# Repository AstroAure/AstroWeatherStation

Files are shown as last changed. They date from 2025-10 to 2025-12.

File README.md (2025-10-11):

# AstroWeatherStation

**AstroWeatherStation** is an open-source weather station that aims at providing a low-cost (~100€) alternative to commercial ones. It also offers full flexibility to how your data are stored and accessed, as well as the possibility to add whatever sensor you want.

To leave a telescope outside permanently (under a dome, or with a waterproof telescope), one needs a weather station to observe the environmental conditions. This allows the telescope to be put in a safe mode if they are dangerous (e.g. rain or dew), or simply to know if observation is possible (absence of clouds).

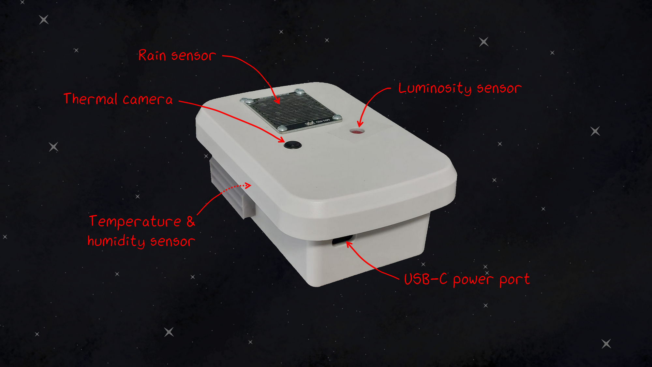
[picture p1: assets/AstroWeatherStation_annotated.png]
Annotated picture of AstroWeatherStation. It is a white box with multiple sensors (rain, luminosity, temperature&humidity and thermal camera) and a USB-C power port.


## Features

AstroWeatherStation hosts multiple different sensors:
* DHT22: Temperature and humidity sensor
* MH-RD: Rain sensor
* MLX90640 110deg: IR Thermal camera (for cloud detection)
* TSL2591: Luminosity sensor (for start/end of observation at dawn/dusk and darkness of night measurement)

It uses the [Grove ecosystem](https://wiki.seeedstudio.com/Grove_System/) to easily connect sensors without any soldering. Sensors that don't use this ecosystem (like the TSL2591 and the MH-RD sensors) can still be connected by using the appropriate adapter cables. AstroWeatherStation uses an ESP32 controller with the Grove Shield and the Grove I2C hub which provides plenty of ports to connect sensors (digital, analog, I2C, UART).

## Hardware

| Component | Quantity | Price | Description |
| :-: | :-: | :-: | :-: |
| [XIAO ESP32-C6 board](https://www.seeedstudio.com/Seeed-Studio-XIAO-ESP32C6-Pre-Soldered-p-6328.html) | 1 | 5.30€ | Controller |
| [Grove Shield](https://www.seeedstudio.com/Grove-Shield-for-Seeeduino-XIAO-p-4621.html) | 1 | 3.90€ | Shield for the ESP32 board |
| [Grove I2C Hub](https://www.seeedstudio.com/Grove-I2C-Hub-6-Port-p-4349.html) | 1 | 1.50€ | Additional I2C ports |
| [DHT22 sensor](https://www.seeedstudio.com/Grove-Temperature-Humidity-Sensor-Pro-AM2302-DHT22.html) | 1 | 7.00€ | Temperature & humidity sensor |
| [MLX90640 110deg](https://www.seeedstudio.com/Grove-Thermal-Imaging-Camera-IR-Array-MLX90640-110-degree-p-4334.html) | 1 | 43.00€ | IR Thermal camera |
| [MH-RD sensor](https://www.berrybase.ch/fr/detail/019234a3bb007361a022dfc33cb3b6cc) | 1 | 1.90€ | Rain sensor |
| [TSL2591 sensor](https://www.berrybase.ch/adafruit-tsl2591-high-dynamic-range-digitaler-licht-sensor) | 1 | 7.50€ | Luminosity sensor |
| [CHD7310WH enclosure](https://www.camdenboss.com/camden-boss/chd7310wh-73-series-ip68-waterproof-enclosure%2C-white%2C-asa-ul94hb%2C-150x100x55mm/c-23/p-24506) | 1 | 25.40€ | Waterproof enclosure |
| [Grove cable](https://www.seeedstudio.com/Grove-Universal-4-Pin-Buckled-20cm-Cable-5-PCs-pack.html) | 3 | 1.70€ | Sensor connection |
| [Grove-Jumper cable](https://www.seeedstudio.com/Grove-4-pin-Female-Jumper-to-Grove-4-pin-Conversion-Cable-5-PCs-per-PAck.html) | 1 | 3.00€ | MH-RD sensor connection |
| [Grove-Qwiic cable](https://www.berrybase.ch/sparkfun-qwiic-grove-adapterkabel-100mm) | 1 | 2.00€ | TSL2591 sensor connection
| [USB-C cable](https://www.berrybase.ch/en/detail/019234a6a33a7045b0129025e8e15021) | 1 | 2.80€ | Power cable
| [Stevenson screen](/hardware/3d-printing/) | 4 | 3D printed | Rain-proof ventilation for inside sensors |
| [MLX90640 support](/hardware/3d-printing/MLX90640%20Support.3mf) | 1 | 3D printed | Support for the MLX90640 thermal camera |
| [TSL2591 support](/hardware/3d-printing/TSL2591%20Support.3mf) | 1 | 3D printed | Support for the TSL2591 sensor |
| [Base plate](/hardware/laser-cutting/Base%20plate.dxf) | 1 | Laser cut | Base plate to hold the electronics

## Code

### ESP32

The weather station is controlled by an ESP32 board ([XIAO ESP32-C6 model](https://www.seeedstudio.com/Seeed-Studio-XIAO-ESP32C6-p-5884.html)). The code, written in MicroPython, for it can be found in [this folder](code/esp32/). It hosts:
* [`boot.py`](code/esp32/boot.py): The booting code which connects the weather station to a WiFi network. If no known network is found, it will host its own WiFi network where you will be able to setup the connection.
* [`main.py`](code/esp32/main.py): The main code that reads the sensor values and upload their values to the `index.html` page.
* [`index.html`](code/esp32/index.html): The raw HTML page that shows the sensor values of the weather station. It is formatted to be used by the [WeatherWatcher INDI library](https://indilib.org/weather/weather-watcher.html), but it can be easily used with an other standard.
* Libraries: [`mlx90640.py`](code/esp32/mlx90640.py), [`tsl2591.py`](code/esp32/tsl2591.py), [`wifimgr.py`](code/esp32/wifimgr.py)
* Test code for individual sensors: [`test_dht22.py`](code/esp32/test/test_dht22.py), [`test_mhrd.py`](code/esp32/test/test_mhrd.py), [`test_mlx90640.py`](code/esp32/test/test_mlx90640.py), [`test_tsl2591.py`](code/esp32/test/test_tsl2591.py)

### RaspberryPi

The weather station publishes its sensor values to an HTML page on the WiFi network to which it is connected. The [`log_astroweatherstation.py`](code/raspberrypi/log_astroweatherstation.py) program recovers the sensor values from this page and sends them to an InfluxDB database to store them. From there, they can be plotted in Grafana for example. This code also saves the IR thermal camera data as an image and in a log file for post-processing.

* To install InfluxDB and Grafana on a RaspberryPi, follow [this tutorial](https://sandyjmacdonald.github.io/2021/12/29/setting-up-influxdb-and-grafana-on-the-raspberry-pi-4/).

* To run the logging code on your RaspberryPi every minute to log the weather station data, you can use the `crontab -e` command and add the following line, where `<PATH-TO-FILE>` should be changed with the absolute path to the Python file:

    ```
    */1 * * * * /usr/bin/python3 <PATH-TO-FILE>/log_astroweatherstation.py &
    ```

## References

* [`wifimgr.py`](https://github.com/tayfunulu/WiFiManager) by [Tayfun ULU](https://github.com/tayfunulu): WiFi manager library *(MIT License)*
* [`tsl2591.py`](https://github.com/mchobby/esp8266-upy/tree/master/tsl2591) by [MCHobby](https://github.com/mchobby): MicroPython library for TSL2591 luminosity sensor *(MIT License)*
* Auto-gain for `tsl2591.py` by [Aurélien Genin](https://github.com/AstroAure) *(MIT License)*
* [`mlx90640.py`](https://github.com/michael-sulyak/micropython-mlx90640) by [Michael Sulyak](https://github.com/michael-sulyak): MicroPython library for MLX90640 IR thermal camera *(MIT License)*

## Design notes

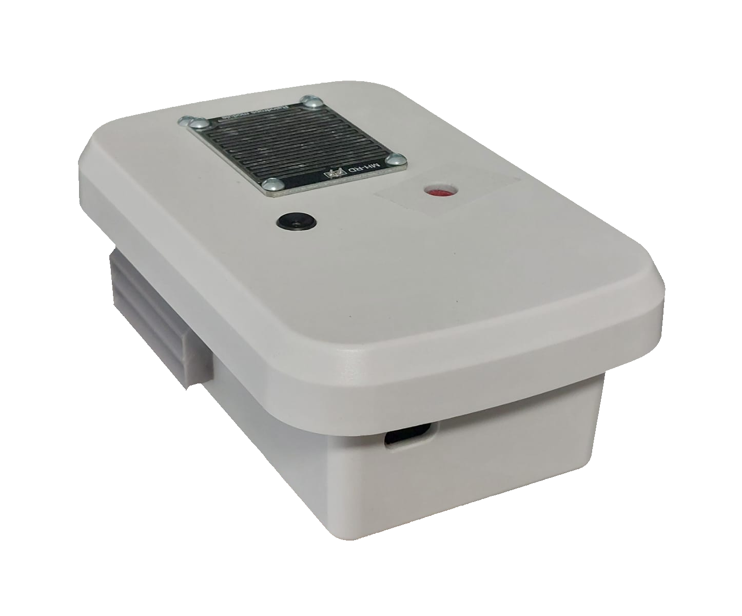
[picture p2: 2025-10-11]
assets/AstroWeatherStation_transparent.png

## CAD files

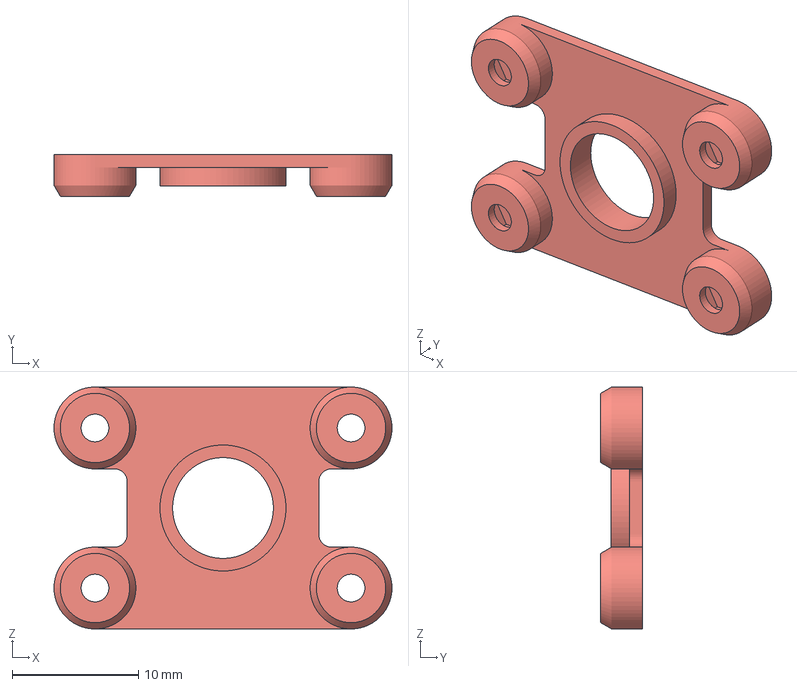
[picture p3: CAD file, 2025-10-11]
hardware/3d-printing/TSL2591 Support.3mf
26.8 x 3.30 x 19.2 mm

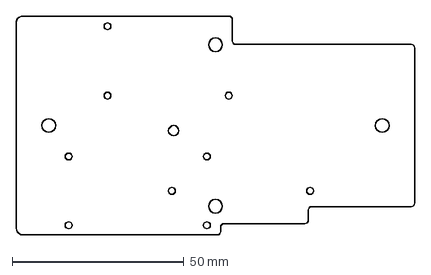
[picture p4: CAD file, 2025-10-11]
hardware/laser-cutting/Base plate.dxf
115.9 x 63.7 mm

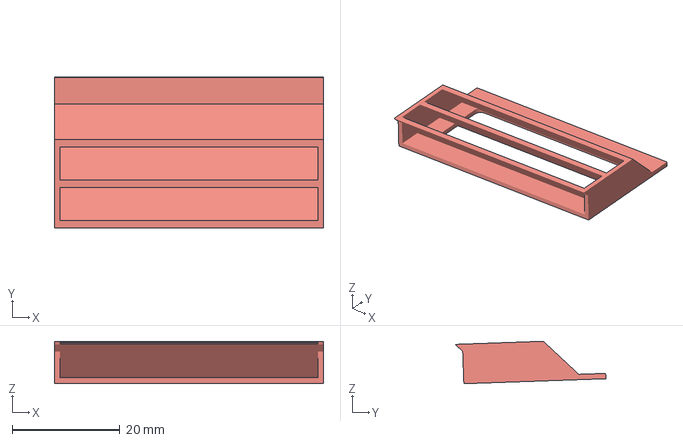
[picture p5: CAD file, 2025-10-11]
hardware/3d-printing/Stevenson Screen 1.3mf
50.0 x 28.0 x 7.89 mm

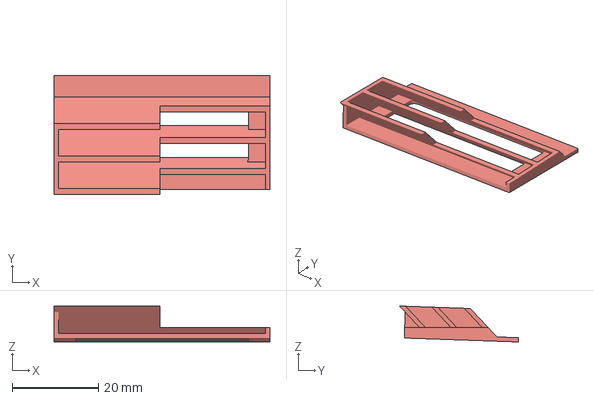
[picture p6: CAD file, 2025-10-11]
hardware/3d-printing/Stevenson Screen 4.3mf
50.0 x 27.5 x 8.33 mm

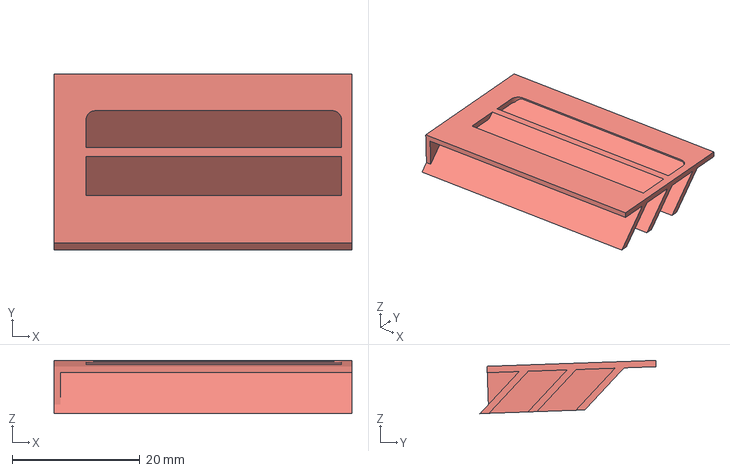
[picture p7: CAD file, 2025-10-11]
hardware/3d-printing/Stevenson Screen 3.3mf
46.6 x 27.5 x 8.33 mm

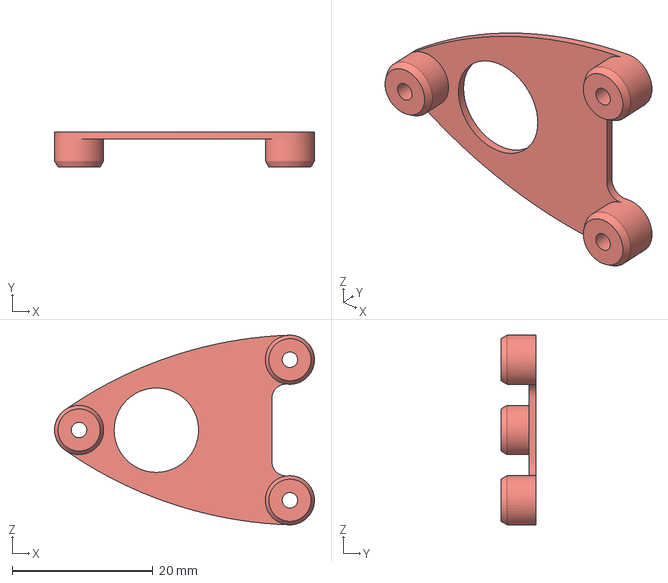
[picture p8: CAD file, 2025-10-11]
hardware/3d-printing/MLX90640 Support.3mf
37.0 x 5.00 x 27.0 mm

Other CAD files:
hardware/3d-printing/Stevenson Screen 2.3mf

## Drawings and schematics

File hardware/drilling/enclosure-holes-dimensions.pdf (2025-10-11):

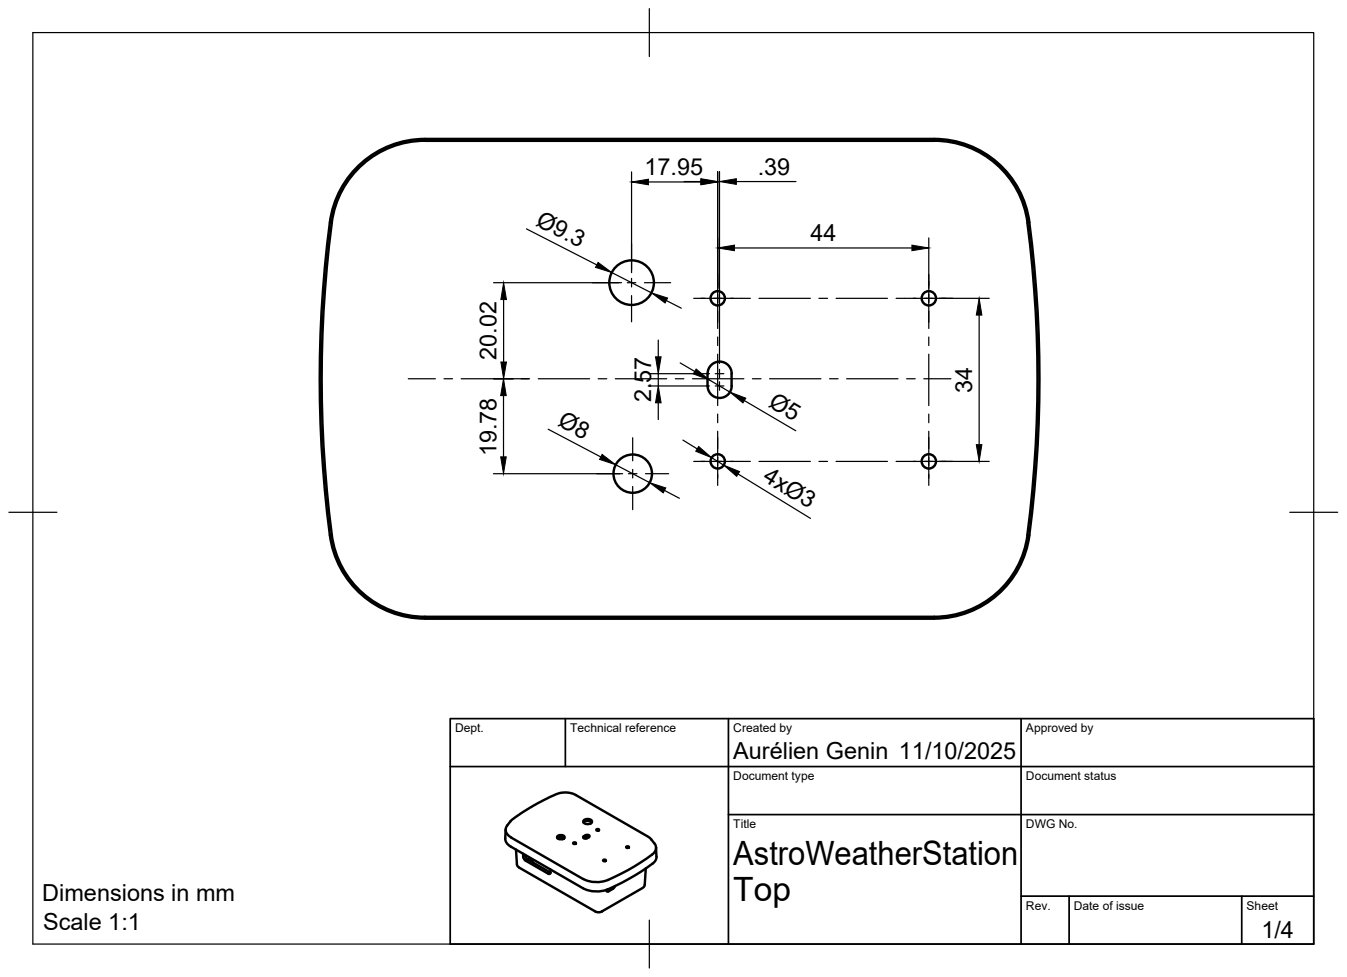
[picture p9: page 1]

Dept. | Technical reference | Created by Aurélien Genin 11/10/2025 | Approved by

Document type | Document status

Title AstroWeatherStation Top | DWG No.

Dimensions in mm
Scale 1:1

Rev. | Date of issue | Sheet

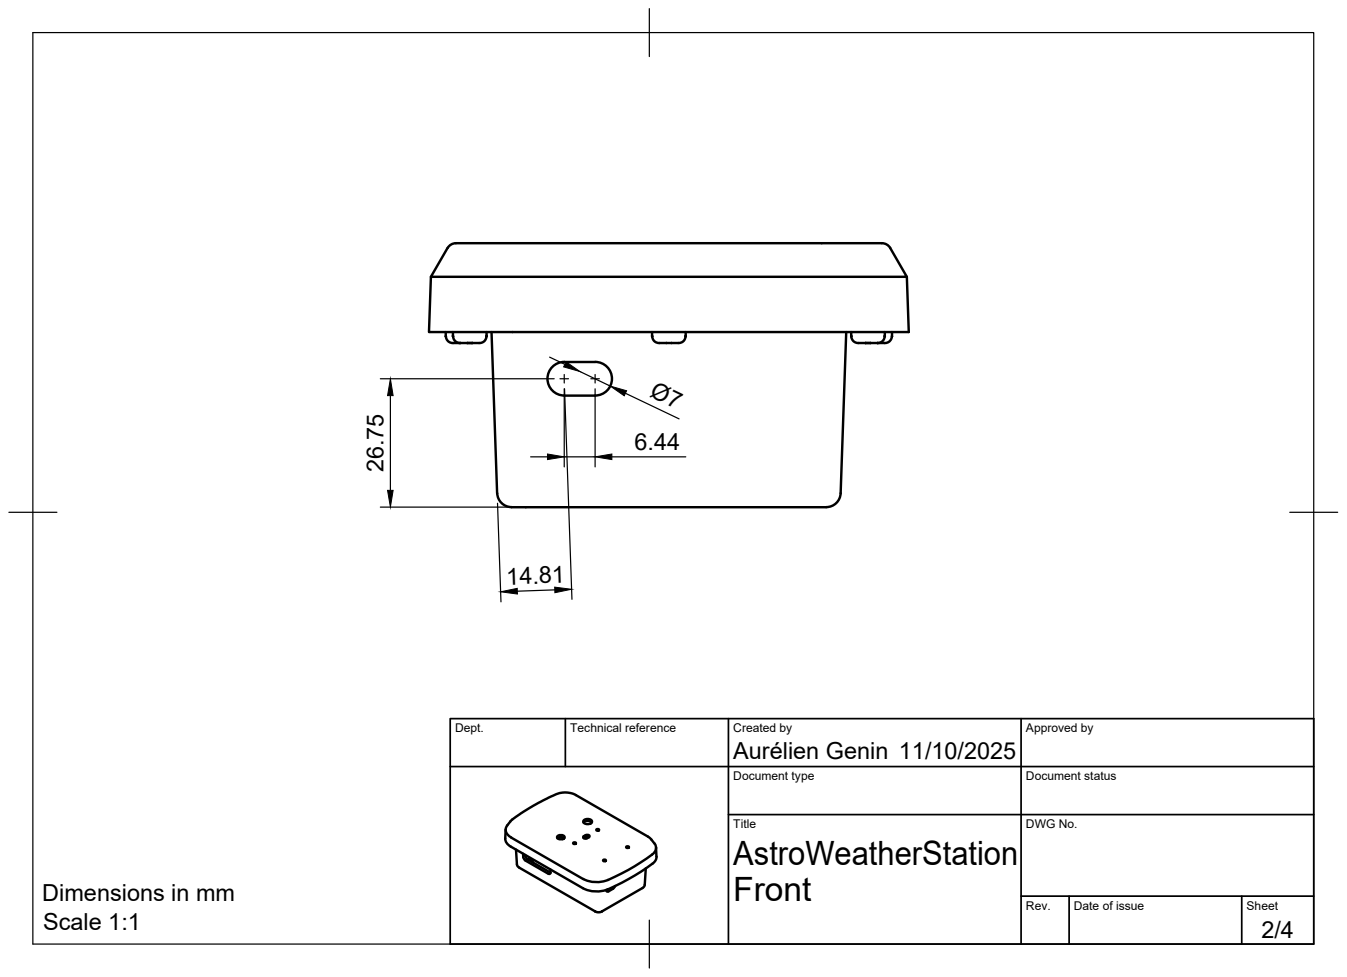
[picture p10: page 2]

Dept. | Technical reference | Created by Aurélien Genin 11/10/2025 | Approved by

Document type | Document status

Title AstroWeatherStation Front | DWG No.

Dimensions in mm

Rev. | Date of issue | Sheet

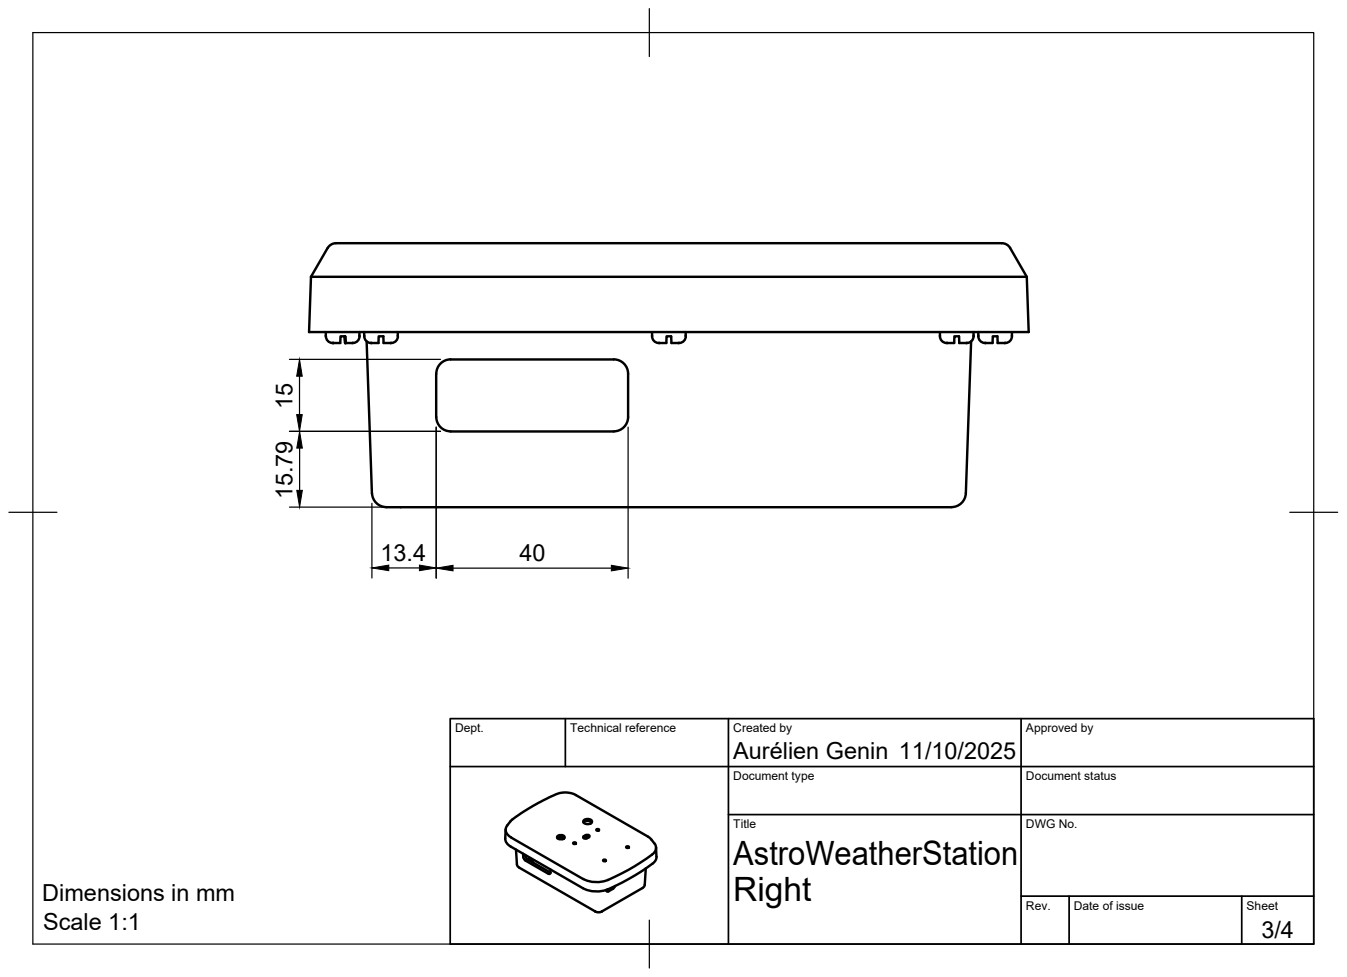
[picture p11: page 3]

Dept. | Technical reference | Created by Aurélien Genin 11/10/2025 | Approved by

Document type | Document status

Title AstroWeatherStation Right | DWG No.

Dimensions in mm

Rev. | Date of issue | Sheet

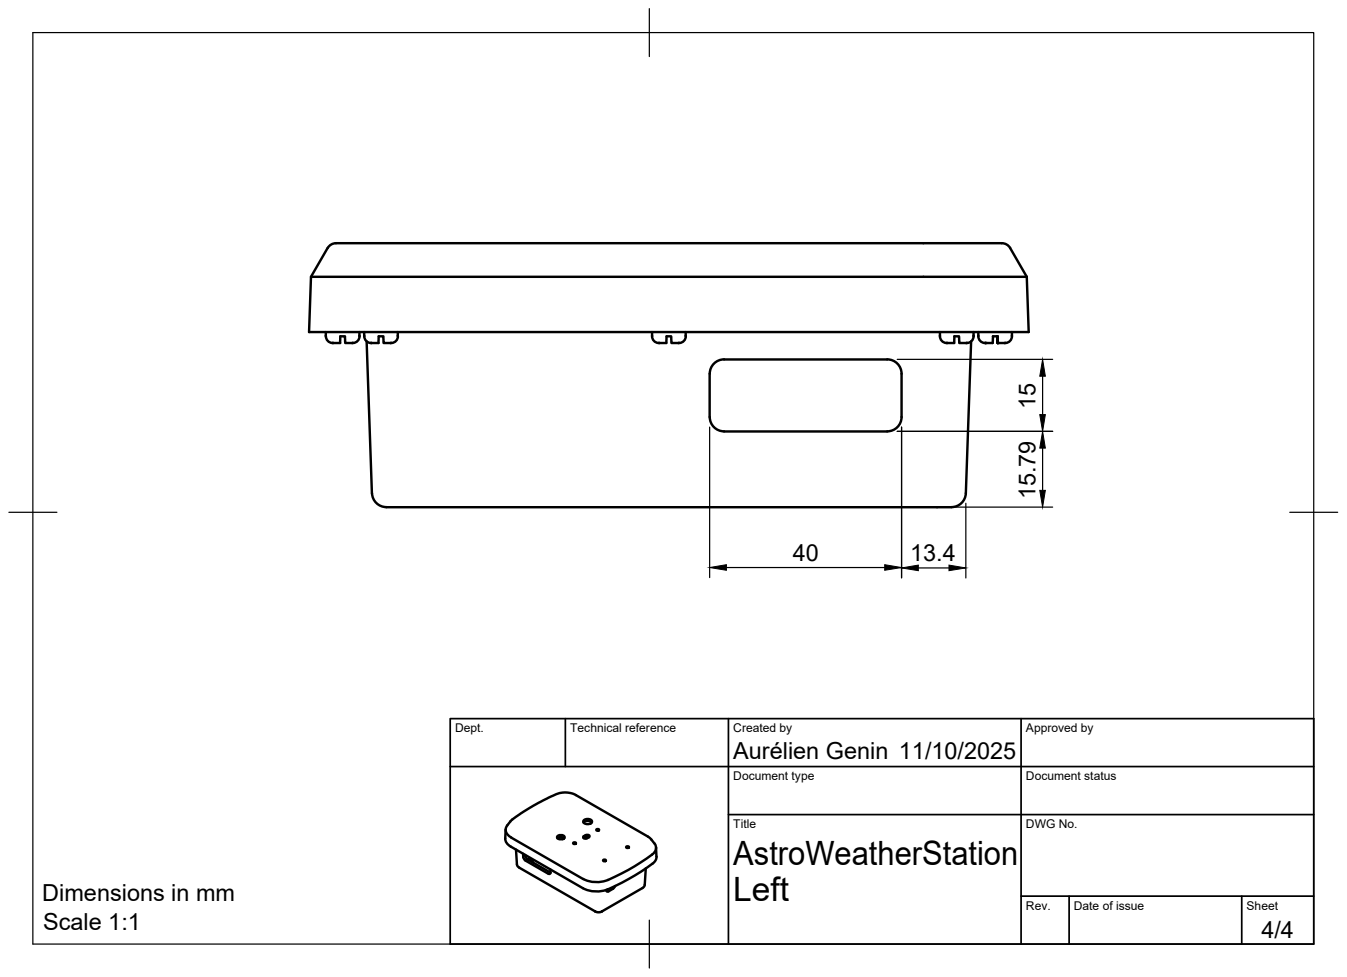
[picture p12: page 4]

Dept. | Technical reference | Created by Aurélien Genin 11/10/2025 | Approved by

Document type | Document status

Title AstroWeatherStation Left | DWG No.

Dimensions in mm

Rev. | Date of issue | Sheet

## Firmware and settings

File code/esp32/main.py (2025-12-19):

import time
import math
from machine import I2C, Pin, RTC, ADC

try:
  import usocket as socket
except:
  import socket
  
import dht
from mlx90640 import MLX90640, RefreshRate, init_float_array
import tsl2591

# To connect to weather station : http://astroweatherstation/index.html or http://10.42.0.126/index.html

# Define time
rtc = RTC()
# Initialize I2C
i2c = I2C(0, sda=Pin(22), scl=Pin(23), freq=400_000)
# DHT22 Temperature+Humidity
DHT22sensor = dht.DHT22(Pin(0))
# MLX90640 Infrared camera
MLX90640sensor = MLX90640(i2c)
MLX90640sensor.refresh_rate = RefreshRate.REFRESH_2_HZ
ir_frame = init_float_array(768)
# MH-RD Rain sensor
MHRDsensor = ADC(Pin(1))
MHRDsensor.width(ADC.WIDTH_12BIT)
MHRDsensor.atten(ADC.ATTN_11DB)
# TSL2591 luminosity
TSL2591 = tsl2591.TSL2591(i2c=i2c)
TSL2591.gain = tsl2591.GAIN_HIGH
TSL2591.integration_time = tsl2591.INTEGRATIONTIME_100MS

def dew_point(tc, rh):
    # tc: Temperature in Celsius
    # rh: Relative humidity
    b = 17.625
    c = 243.04 # degC
    gamma = math.log(rh/100) + b*tc/(c+tc)
    td = c*gamma/(b-gamma)
    return td

def cutout_frame(data, x, y, size_x, size_y, w=32, h=24):
    half_x = size_x // 2
    half_y = size_y // 2
    cut = []
    for i in range(-half_x, half_x + 1):
        for j in range(-half_y, half_y + 1):
            xi = min(max(x + i, 0), w - 1)
            yj = min(max(y + j, 0), h - 1)
            cut.append(data[w*yj + xi])
    return cut

def mean(l):
    n = len(l)
    m = 0
    for i in range(n):
        m += l[i]
    return m/n

# Establish connection
s = socket.socket(socket.AF_INET, socket.SOCK_STREAM)
try:
    s.bind(('', 80))
except OSError:
    continue
s.listen(5)

oldsec = -1
oldmins = -1
while True:
    # Get time
    tnow = rtc.datetime()
    year = str(tnow[0])
    month = str(tnow[1]) if tnow[1]>=10 else '0'+str(tnow[1])
    day = str(tnow[2]) if tnow[2]>=10 else '0'+str(tnow[2])
    hour = str(tnow[4]) if tnow[4]>=10 else '0'+str(tnow[4])
    minute = str(tnow[5]) if tnow[5]>=10 else '0'+str(tnow[5])
    sec = int(tnow[6]) if tnow[6]>=10 else '0'+str(tnow[6])
    str_date_time = f"{year}-{month}-{day}T{hour}:{minute}:{sec}"

    # Update every 10s
    if ((int(sec) - int(oldsec) > 10) or (minute != oldmins)):
        oldsec = sec
        oldmins = minute
        
        # DHT22 Temperature+Humidity
        DHT22sensor.measure()
        tc = DHT22sensor.temperature()
        rh = DHT22sensor.humidity()
        td = dew_point(tc, rh)

        # MLX90640 Infrared camera
        MLX90640sensor.get_frame(ir_frame)
        MLX90640sensor.get_frame(ir_frame) # Read twice to solve checkerboard issue
        ir_center = cutout_frame(ir_frame, 16, 12, 5, 5)
        temp_sky = mean(ir_center)
        # Heuristic to check in real conditions
        if (temp_sky < -8.):
            clouds = 0
        elif (temp_sky < 0.):
            clouds = (temp_sky + 8.)/8
        else:
            clouds = 1
            
        # MHRD Rain sensor
        rain_sens = MHRDsensor.read()
        if (rain_sens > 3_000):
            rain = 0
        elif (rain_sens > 2_800):
            rain = -(rain_sens - 3_000)/(3_000-2_800)
        else:
            rain = 1
            
        # TSL2591 luminosity
        tsl_lux = TSL2591.lux_auto_gain
        tsl_ir = TSL2591.infrared
        tsl_vis = TSL2591.visible
        tsl_full = TSL2591.full_spectrum
        
        # Write HTML file
        print(str_date_time)
        file = open("index.html", "w")
        file.write('<html>\n<head><title>AstroWeatherStation</title></head>\n<body>\n')
        file.write('timestamp=' + str_date_time + ' <br />\n')
        file.write(f"ir_sky={temp_sky:.2f} <br />\n")
        file.write(f"clouds={clouds:.2f} <br />\n") # WeatherWatcher keyword
#         file.write('forecast={0:.3f}'.format(clouds) + ' <br />\n') # WeatherWatcher keyword
        file.write(f"temperature={tc:.2f} <br />\n") # WeatherWatcher keyword
        file.write(f"humidity={rh:.2f} <br />\n") # WeatherWatcher keyword
        file.write(f"dew_point={td:.2f} <br />\n")
        file.write(f"rain_sensor={rain_sens:.0f} <br />\n")
        file.write(f"precip={rain:.2f} <br />\n") # WeatherWatcher keyword
#         file.write(f"wind={wind:.2f} <br />\n") # WeatherWatcher keyword
#         file.write(f"gust={gust:.2f} <br />\n") # WeatherWatcher keyword
#         file.write(f"pressure={pressure:.2f} <br />\n") # WeatherWatcher keyword
        file.write(f"luminosity={tsl_lux:.5f} <br />\n")
        file.write('</body>\n')
        file.write('<ir_image>\n')
        file.write(f"ir_image={str(ir_frame)} <br />\n")
        file.write('</ir_image>\n')
        file.write('</html>\n')
        file.close()

    # Upload file
    file = open("index.html", "r")
    response = file.read()
    file.close()
    
    conn, addr = s.accept()
    print('Got a connection from %s' % str(addr))
    request = conn.recv(1024)
    conn.send('HTTP/1.1 200 OK\n')
    conn.send('Content-Type: text/html\n')
    conn.send('Connection: close\n\n')
    conn.sendall(response)
    conn.close()
